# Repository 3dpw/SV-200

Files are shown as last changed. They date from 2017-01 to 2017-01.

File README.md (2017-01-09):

#SV-200
####The Simplest 3D Printer with Liner Guideway (full 200x200x200mm printable area)

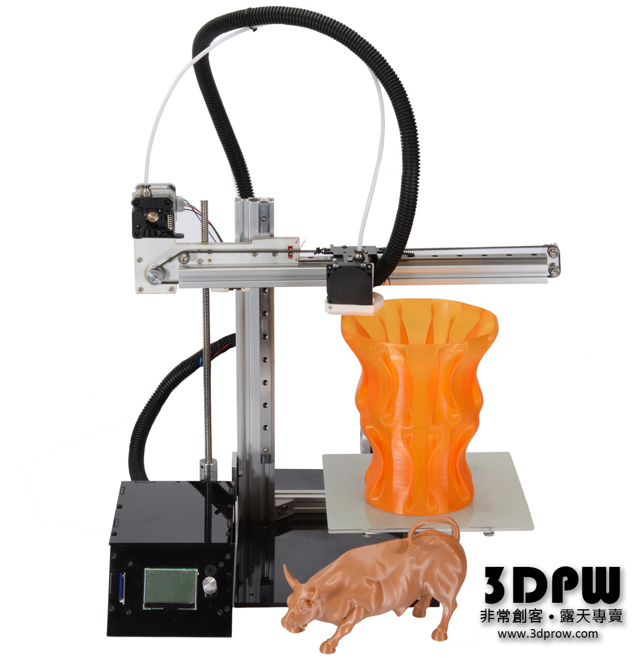
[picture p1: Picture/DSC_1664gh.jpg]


###Intro
SV-200 is designed by Taiwan 3DPW Synmao Techlogogy Enterprise Co., Ltd.
It has the simplest cartesian system design with solid structure by aluminum extrusions. SV-200 has full 200x200x200mm printable area.
The most attractive design is SV-200 is using liner guideway for all 3 axis and Z axis is using 8mm T-type leadscrew.
These design really improve print quality a lot.
The hotend is also a new design with Teflon tube staight to the nozzle for no fliament jam.
SV-200 is controlled by seperating control box with 128x64 full graphic LCD. The control box is off from the printer strucutre. This brings benfit when you need flexible space to operate your printer.
This great design is now open source. You are welcome to join this project and improve even more.

###General Spec
200x200x200 printable area  
MGN12H mini Liner guideway for X and Y  
8mm Leadscrew for Z
Remote extruder system

###BOM (Last update 2017/01/03 01:15)
#####Electronics
MKS Gen V1.4  
Endstop (Switch) x2  
Endstop (IR optical) x1  
Fan 3010 DC12V x1 (for control box chassis)  
Fan BFB04512HHA 45mm DC12V (parts cooling)  
Power Switch x1  
Power jack 2.5mm female x1  
Cable 4PIN to 4PIN 100cm x4 (steppers)  
Cable 4PIN to 3PIN 100cm x2 (Endstop switch)  
Cable 3PIN to 3PIN 100cm x1 (Endstop IR optical)  
Bowden Hotend set x1  
USB cable type-B to type-C x1
Power adapter DC12V 5A  
#####Mechnical
2020 aluminum extrusion L370mm x1 (X axis)  
2040 aluminum extrusion L300mm x1 (Y axis)  
2040 aluminum extrusion L350mm x1 (Z axis)  
2028 aluminum extrusion 90 degree corner bracket x2  
2020 aluminum extrusion 90 degree corner bracket x3  
Liner guideway MGN12H 250mm with block x3 sets (All 3 axis)  
Leadscrew with square nut, 4mm lead x1 (Z axis)  
Coupler 5x8 x1  
2GT Belt about 1500mm x1 (X and Y)  
Acrylic (6mm) or aluminum board (3mm) laser cut from a CAD files.  
Acrylic (3mm) laser cut for Control box  
NEMA17 (42mm) L40 Stepper x4 (XYZ and E axis)  
Stepper motor L bracket x1
Teflon tube 2x4 L50 x1  
Extruder (Bowden) x1  
105ZZ bearing x12 (belt idler)
Pully GT2 6mm 20 tooth x 2
Spring 5x18x0.5mm x4
Screws/Washer List
Hex socket  
M3x 6 x4 (X and Z endstop)  
M3x 8 x 58:

	X motor x4
	Y motor x4
	Z motor x4
    X,Z,E axis board x3
	Y motor plate x4
	Y idler plate x4
	liner guideway x9
	liner guideway carriage x16
    Leadscrew nut x4
	Y endstop x2
    Hotend x4

M3x 3 plastic washer x2 (Y endstop)  
M3x25 flat x4  
M5x25 x 6 + wasger x12 (belt idlers)  
M5 nut x12  
T-type nut for 20mm aluminum extrusion x14

	X,Z,E axis board x3
    X liner guideway x3
    Y liner guideway x3
    Z liner guideway x3
    Z motor bracket x2

M3 thumb nut x4  
#####Control box:
M3x16 x22 (button hex socket):

	Chassic x14
    Control board x4
    LCD control panel x4
M3 nut x18:

	Chassis x14
    Control board x4

M3x 3 plastic washer x2:

	Control board x4
    LCD control panel x8
M3 frange nut x4 (LCD cotrol panel)  

(To be complete)

##Where to buy
Parts and DIY sets to be available in 3DPW before Chinese New Year.

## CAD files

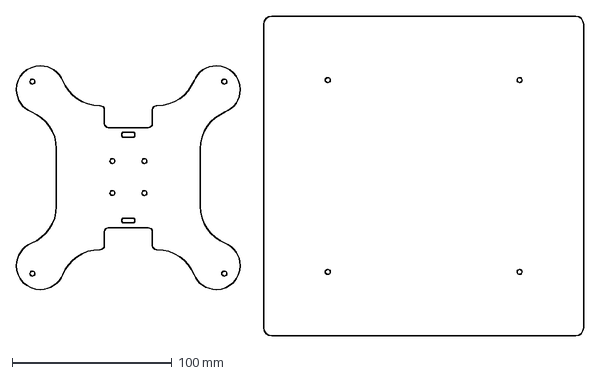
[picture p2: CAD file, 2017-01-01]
CAD/Y axis and print plate.dxf
354.7 x 200.0 mm

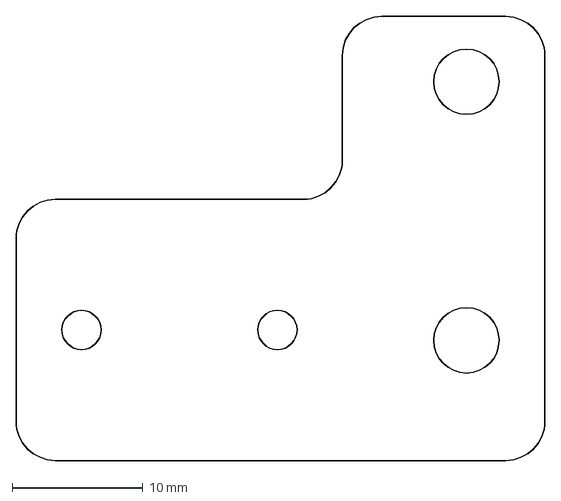
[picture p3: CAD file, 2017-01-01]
CAD/X axis idler board.dxf
40.5 x 34.0 mm

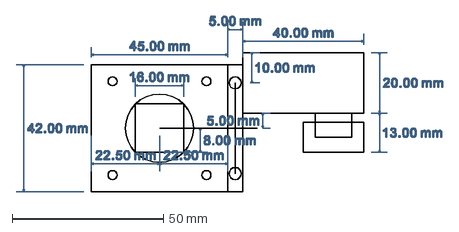
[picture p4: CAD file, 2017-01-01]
CAD/Z axis alignment.dxf
141.0 x 58.0 mm

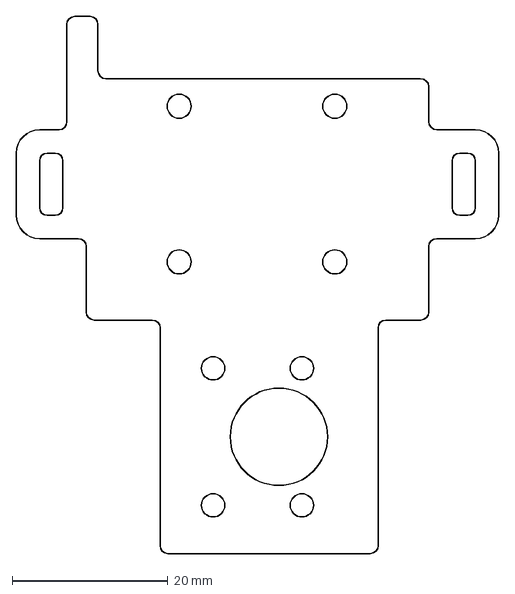
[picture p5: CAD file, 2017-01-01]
CAD/X axis carriage.dxf
62.0 x 69.0 mm

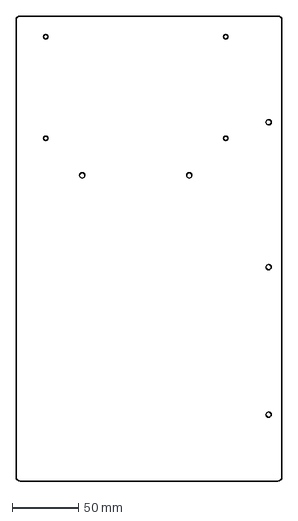
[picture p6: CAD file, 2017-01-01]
CAD/Backplate.dxf
200.0 x 350.0 mm

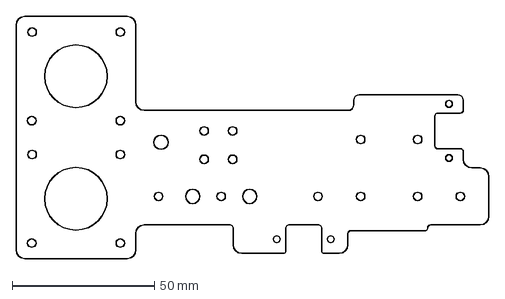
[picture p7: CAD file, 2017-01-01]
CAD/XZE 3in1 board.dxf
166.0 x 85.0 mm

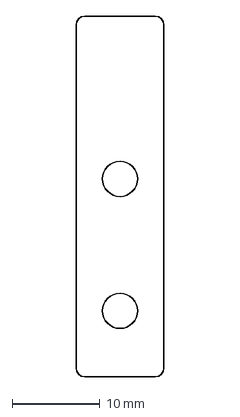
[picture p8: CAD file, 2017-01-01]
CAD/Z endstop trigger.dxf
10.0 x 41.0 mm

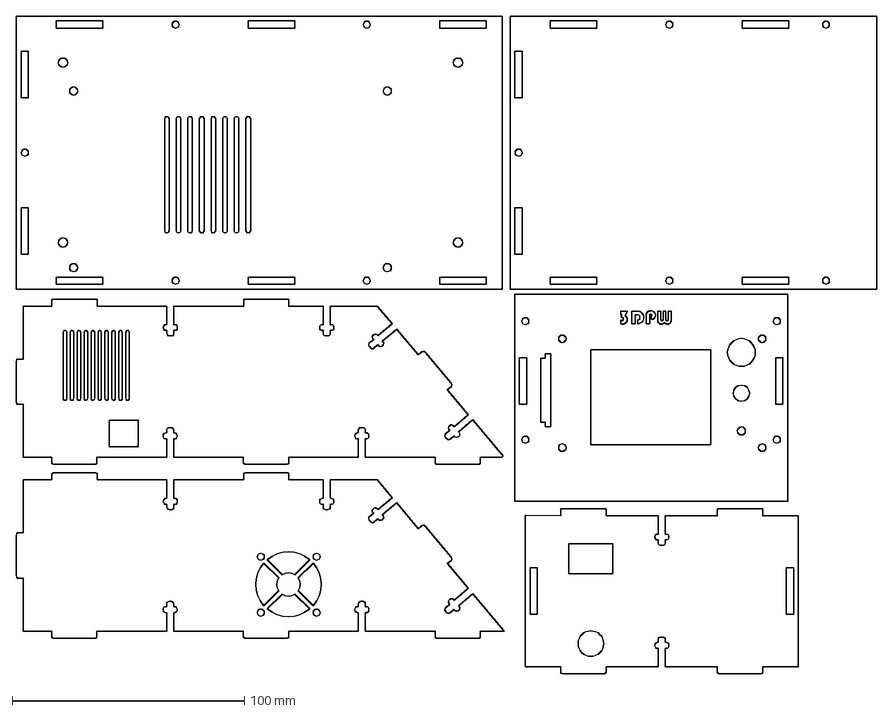
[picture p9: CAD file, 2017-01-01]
CAD/12864 Mini LCD Control box.dxf
370.1 x 282.9 mm

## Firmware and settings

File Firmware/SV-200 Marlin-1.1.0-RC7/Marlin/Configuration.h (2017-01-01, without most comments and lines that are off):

#define CONFIGURATION_H
#define CONFIGURATION_H_VERSION 010100
#define STRING_CONFIG_H_AUTHOR "(none, default config)" // Who made the changes.
#define SHOW_BOOTSCREEN
#define STRING_SPLASH_LINE1 SHORT_BUILD_VERSION // will be shown during bootup in line 1
#define STRING_SPLASH_LINE2 WEBSITE_URL         // will be shown during bootup in line 2
#define SERIAL_PORT 0
#define BAUDRATE 250000
  #define MOTHERBOARD BOARD_RAMPS_14_EFB
#define EXTRUDERS 1
#define POWER_SUPPLY 1
#define TEMP_SENSOR_0 1
#define TEMP_SENSOR_1 0
#define TEMP_SENSOR_2 0
#define TEMP_SENSOR_3 0
#define TEMP_SENSOR_BED 0
#define MAX_REDUNDANT_TEMP_SENSOR_DIFF 10
#define TEMP_RESIDENCY_TIME 10  // (seconds)
#define TEMP_HYSTERESIS 3       // (degC) range of +/- temperatures considered "close" to the target one
#define TEMP_WINDOW     1       // (degC) Window around target to start the residency timer x degC early.
#define TEMP_BED_RESIDENCY_TIME 10  // (seconds)
#define TEMP_BED_HYSTERESIS 3       // (degC) range of +/- temperatures considered "close" to the target one
#define TEMP_BED_WINDOW     1       // (degC) Window around target to start the residency timer x degC early.
#define HEATER_0_MINTEMP 5
#define HEATER_1_MINTEMP 5
#define HEATER_2_MINTEMP 5
#define HEATER_3_MINTEMP 5
#define BED_MINTEMP 5
#define HEATER_0_MAXTEMP 275
#define HEATER_1_MAXTEMP 275
#define HEATER_2_MAXTEMP 275
#define HEATER_3_MAXTEMP 275
#define BED_MAXTEMP 150
#define PIDTEMP
#define BANG_MAX 255 // limits current to nozzle while in bang-bang mode; 255=full current
#define PID_MAX BANG_MAX // limits current to nozzle while PID is active (see PID_FUNCTIONAL_RANGE below); 255=full current
  #define PID_FUNCTIONAL_RANGE 10 // If the temperature difference between the target temperature and the actual temperature
  #define PID_INTEGRAL_DRIVE_MAX PID_MAX  //limit for the integral term
  #define K1 0.95 //smoothing factor within the PID
  #define  DEFAULT_Kp 22.2
  #define  DEFAULT_Ki 1.08
  #define  DEFAULT_Kd 114
#define MAX_BED_POWER 255 // limits duty cycle to bed; 255=full current
#define PREVENT_DANGEROUS_EXTRUDE
#define PREVENT_LENGTHY_EXTRUDE
#define EXTRUDE_MINTEMP 170
#define EXTRUDE_MAXLENGTH (X_MAX_LENGTH+Y_MAX_LENGTH) //prevent extrusion of very large distances.
#define THERMAL_PROTECTION_HOTENDS // Enable thermal protection for all extruders
#define THERMAL_PROTECTION_BED     // Enable thermal protection for the heated bed
#define USE_XMIN_PLUG
#define USE_YMIN_PLUG
#define USE_ZMIN_PLUG
#define ENDSTOPPULLUPS // Comment this out (using // at the start of the line) to disable the endstop pullup resistors
#define X_MIN_ENDSTOP_INVERTING false // set to true to invert the logic of the endstop.
#define Y_MIN_ENDSTOP_INVERTING false // set to true to invert the logic of the endstop.
#define Z_MIN_ENDSTOP_INVERTING false // set to true to invert the logic of the endstop.
#define X_MAX_ENDSTOP_INVERTING false // set to true to invert the logic of the endstop.
#define Y_MAX_ENDSTOP_INVERTING false // set to true to invert the logic of the endstop.
#define Z_MAX_ENDSTOP_INVERTING false // set to true to invert the logic of the endstop.
#define Z_MIN_PROBE_ENDSTOP_INVERTING false // set to true to invert the logic of the endstop.
#define X_PROBE_OFFSET_FROM_EXTRUDER 10  // X offset: -left  +right  [of the nozzle]
#define Y_PROBE_OFFSET_FROM_EXTRUDER 10  // Y offset: -front +behind [the nozzle]
#define Z_PROBE_OFFSET_FROM_EXTRUDER 0   // Z offset: -below +above  [the nozzle]
#define XY_PROBE_SPEED 8000
#define Z_PROBE_SPEED_FAST HOMING_FEEDRATE_Z
#define Z_PROBE_SPEED_SLOW (Z_PROBE_SPEED_FAST / 2)
#define Z_MIN_PROBE_USES_Z_MIN_ENDSTOP_PIN
#define Z_PROBE_DEPLOY_HEIGHT 15 // Raise to make room for the probe to deploy / stow
#define Z_PROBE_TRAVEL_HEIGHT 5  // Raise between probing points.
#define Z_PROBE_OFFSET_RANGE_MIN -20
#define Z_PROBE_OFFSET_RANGE_MAX 20
#define X_ENABLE_ON 0
#define Y_ENABLE_ON 0
#define Z_ENABLE_ON 0
#define E_ENABLE_ON 0 // For all extruders
#define DISABLE_X false
#define DISABLE_Y false
#define DISABLE_Z false
#define DISABLE_E false // For all extruders
#define DISABLE_INACTIVE_EXTRUDER true //disable only inactive extruders and keep active extruder enabled
#define INVERT_X_DIR false
#define INVERT_Y_DIR true
#define INVERT_Z_DIR false
#define INVERT_E0_DIR false
#define INVERT_E1_DIR false
#define INVERT_E2_DIR false
#define INVERT_E3_DIR false
#define X_HOME_DIR -1
#define Y_HOME_DIR -1
#define Z_HOME_DIR -1
#define min_software_endstops true // If true, axis won't move to coordinates less than HOME_POS.
#define max_software_endstops true  // If true, axis won't move to coordinates greater than the defined lengths below.
#define X_MIN_POS 0
#define Y_MIN_POS 0
#define Z_MIN_POS 0
#define X_MAX_POS 200
#define Y_MAX_POS 200
#define Z_MAX_POS 200
#define HOMING_FEEDRATE_XY (50*60)
#define HOMING_FEEDRATE_Z  (4*60)
#define DEFAULT_AXIS_STEPS_PER_UNIT   {80,80,4000,500}  // default steps per unit for Ultimaker
#define DEFAULT_MAX_FEEDRATE          {300, 300, 5, 25}    // (mm/sec)
#define DEFAULT_MAX_ACCELERATION      {3000,3000,100,10000}    // X, Y, Z, E maximum start speed for accelerated moves. E default values are good for Skeinforge 40+, for older versions raise them a lot.
#define DEFAULT_ACCELERATION          3000    // X, Y, Z and E acceleration in mm/s^2 for printing moves
#define DEFAULT_RETRACT_ACCELERATION  3000    // E acceleration in mm/s^2 for retracts
#define DEFAULT_TRAVEL_ACCELERATION   3000    // X, Y, Z acceleration in mm/s^2 for travel (non printing) moves
#define DEFAULT_XYJERK                20.0    // (mm/sec)
#define DEFAULT_ZJERK                 0.4     // (mm/sec)
#define DEFAULT_EJERK                 5.0    // (mm/sec)
#define HOST_KEEPALIVE_FEATURE        // Disable this if your host doesn't like keepalive messages
#define DEFAULT_KEEPALIVE_INTERVAL 2  // Number of seconds between "busy" messages. Set with M113.
#define PREHEAT_1_TEMP_HOTEND 180
#define PREHEAT_1_TEMP_BED     70
#define PREHEAT_1_FAN_SPEED     0 // Value from 0 to 255
#define PREHEAT_2_TEMP_HOTEND 240
#define PREHEAT_2_TEMP_BED    110
#define PREHEAT_2_FAN_SPEED     0 // Value from 0 to 255
#define PRINTJOB_TIMER_AUTOSTART
#define LCD_LANGUAGE en
#define DISPLAY_CHARSET_HD44780 JAPANESE
#define SOFT_PWM_SCALE 0
#define SERVO_DELAY 300
#define DEFAULT_NOMINAL_FILAMENT_DIA 3.00  //Enter the diameter (in mm) of the filament generally used (3.0 mm or 1.75 mm) - this is then used in the slicer software.  Used for sensor reading validation

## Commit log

2017-01-01 First upload firmware
    Initial upload
    [Configuration.h, Configuration_adv.h]
2017-01-01 2D DXF first upload
    Acrylic or aluminum board laser cut boards
    [12864 Mini LCD Control box.dxf, Backplate.dxf, X axis carriage.dxf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]

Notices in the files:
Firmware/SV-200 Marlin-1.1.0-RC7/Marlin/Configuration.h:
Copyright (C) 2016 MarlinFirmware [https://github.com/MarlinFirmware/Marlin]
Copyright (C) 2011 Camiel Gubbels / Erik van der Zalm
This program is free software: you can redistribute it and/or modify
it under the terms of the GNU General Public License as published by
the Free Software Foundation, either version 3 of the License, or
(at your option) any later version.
